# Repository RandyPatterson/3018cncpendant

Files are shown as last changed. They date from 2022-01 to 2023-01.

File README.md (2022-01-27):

# Pendant Controller for 3018 CNC
An Arduino based Handwheel Pendant for a generic 3018 CNC.  Allows you to easily move the X, Y and Z axis using the handwheel.  You can dial in the exact position using the 0.1 mm/step or quickly move to a new location using the 1.0 mm/step buttons.

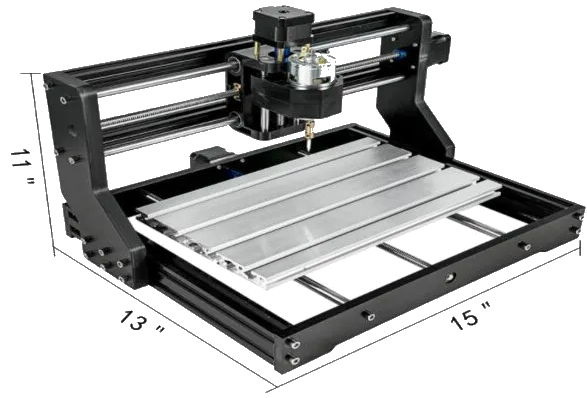
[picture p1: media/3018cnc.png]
3018 CNC

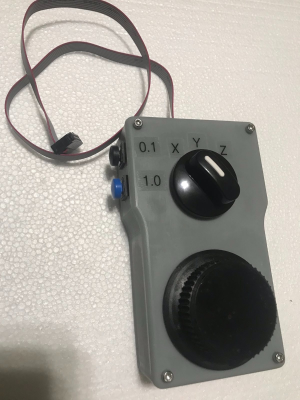
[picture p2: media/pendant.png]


### Required Hardware
1. 1x Arduino Pro Mini (or compatible)
1. 1x KY-040 Rotary Encoder ([Amazon](https://www.amazon.com/gp/product/B07D356LRH/ref=ppx_yo_dt_b_asin_title_o04_s00?ie=UTF8&psc=1))
1. 1x SP3T Rotary Switch ([Amazon](https://www.amazon.com/gp/product/B018LYU3OO/ref=ppx_yo_dt_b_asin_title_o01_s00?ie=UTF8&psc=1))
1. 4x M3 x 6mm screws
1. 4x M3 x 5mm x 3mm thread inserts ([Amazon](https://www.amazon.com/cSeao-120pcs-Inserted-Knurled-Embedded/dp/B07D683Q26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]))
1. 2x 12mm momentary SPST square push buttons
1. 1x 2x4 (8 pin) 2.54mm pitch flat ribbon cable
1. 1x 2x4 2.54mm pitch connector (optional, for PCB) ([Amazon](https://www.amazon.com/gp/product/B07WPBQPBT/ref=ppx_yo_dt_b_asin_title_o03_s00?ie=UTF8&psc=1))

### This repo includes
1. [/src](/src) = Source code for an Arduino Pro Mini (PlatformIO)
1. [/pcb](/pcb) = Schematic and PCB layout (KiCad)
1. [/model](/model) = STEP, Fusion360 and 3MF files for 3D printing the case and handwheel

## Source Code
Build using the PlatformIO plugin for VS Code.  Targeting Arduino Pro Mini but any board can be used as long as it has at least 7 open IO Ports

## Schematic (Optional) 
Optional schematic and PCB to help cleanup the wiring.  Bypass capacitors are used on the encoder data lines to help reduce switch bounce.

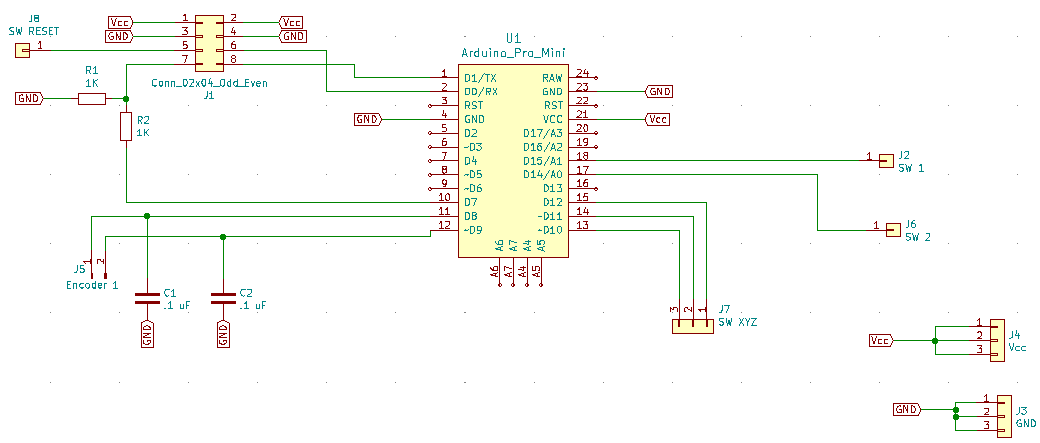
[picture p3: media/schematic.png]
Schematic

### PCB
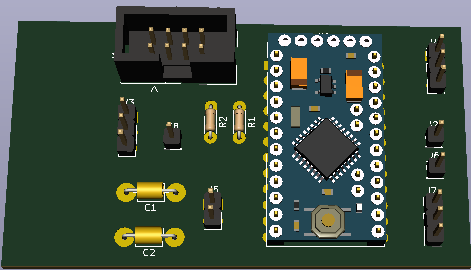
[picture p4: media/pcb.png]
Circuit


## Models
3D Models for case and handwheel to 3D print.  I used a resin printer but the models should be easily printable on FDM Printers.  The Models directory includes the SMF files to print unmodified and STEP files included for situations where you want to modify the 3D models in your favorite CAD program.  Fusion 360 files also included.

### Case & Handwheel Models

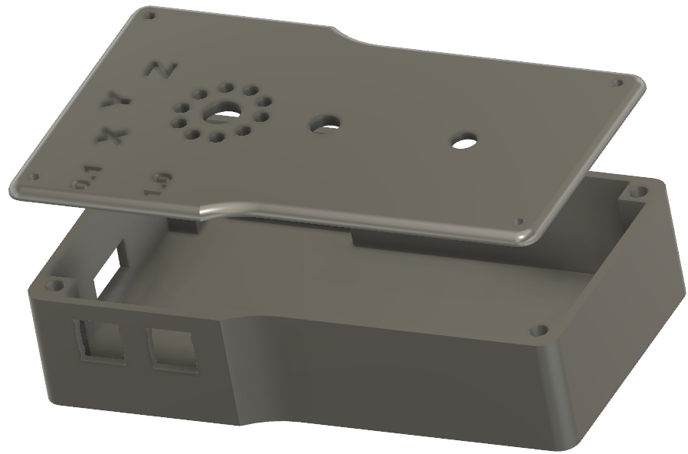
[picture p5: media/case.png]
Case
 
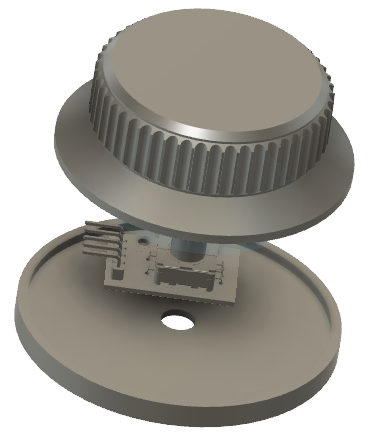
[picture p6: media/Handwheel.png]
Handwheel


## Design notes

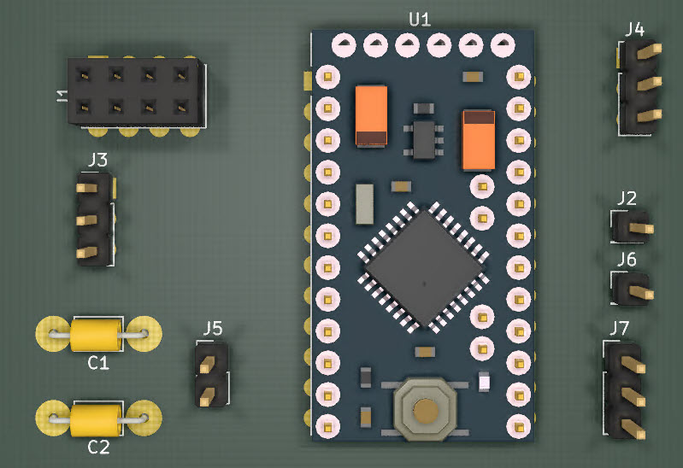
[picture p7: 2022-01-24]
media/circuit_3d.jpg

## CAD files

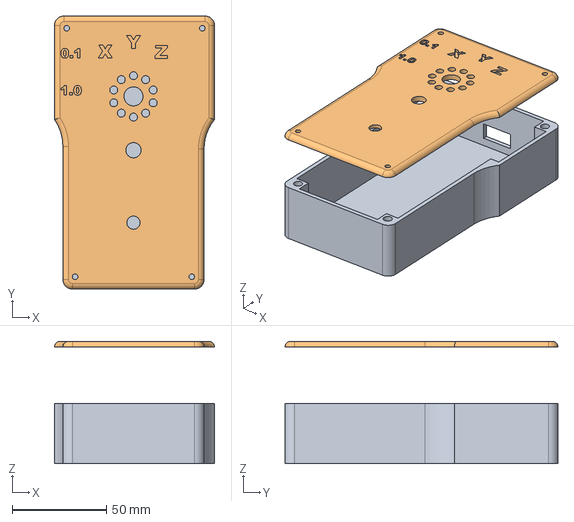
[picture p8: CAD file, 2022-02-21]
models/case/3018 pendant case.step
85.0 x 145.0 x 65.0 mm

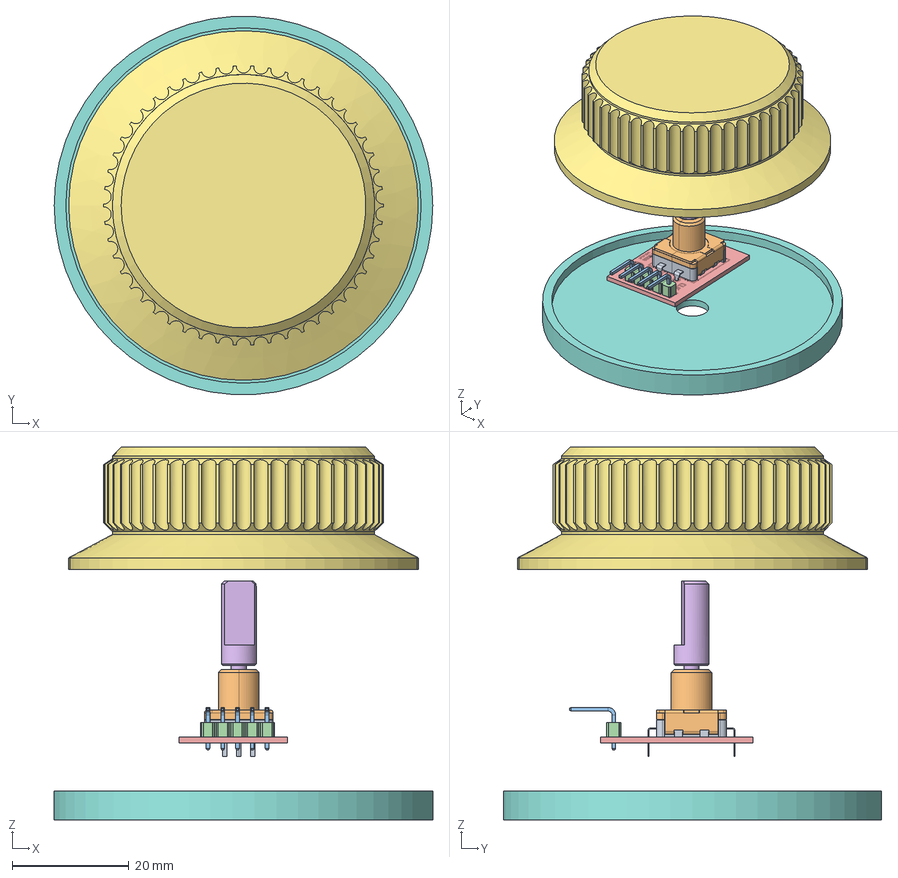
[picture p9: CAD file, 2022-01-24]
models/handwheel/Handwheel.step
65.0 x 64.9 x 64.0 mm
Rotary Encoder
2.54 5PIN 90
pcb
D-handle

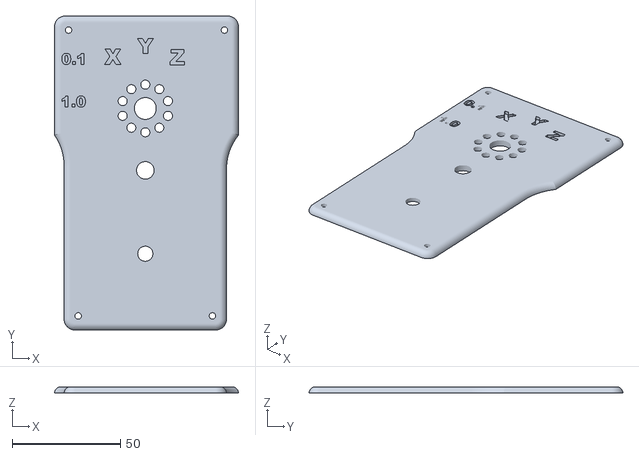
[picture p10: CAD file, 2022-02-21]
models/case/Top.stl
85.0 x 145.0 x 3.00

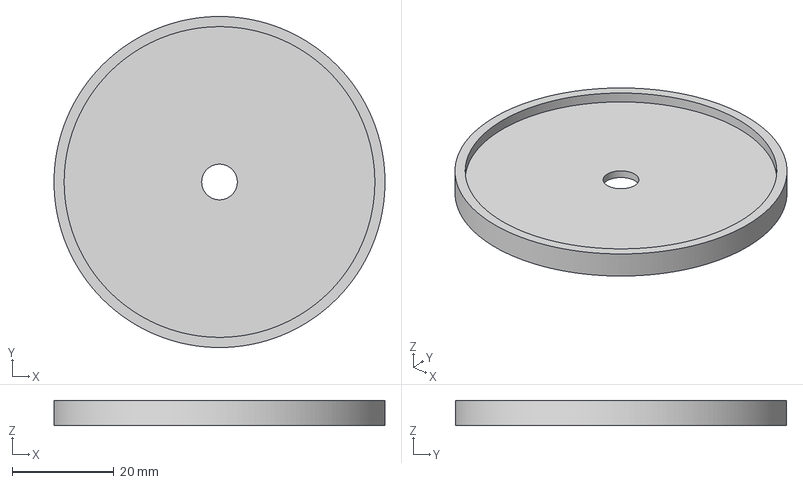
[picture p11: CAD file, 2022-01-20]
models/handwheel/base.3mf
65.0 x 65.0 x 5.00 mm

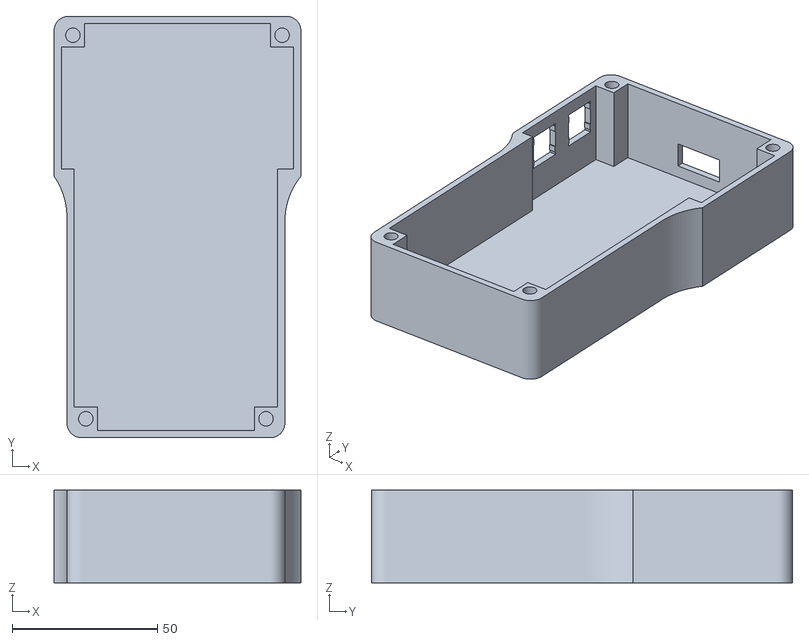
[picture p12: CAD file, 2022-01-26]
models/case/Bottom.stl
85.0 x 145.0 x 32.0

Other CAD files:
models/case/3018 pendant case.f3d
models/handwheel/Handwheel.3mf
models/handwheel/Handwheel.f3d
models/handwheel/Handwheel.stl
models/handwheel/base.stl

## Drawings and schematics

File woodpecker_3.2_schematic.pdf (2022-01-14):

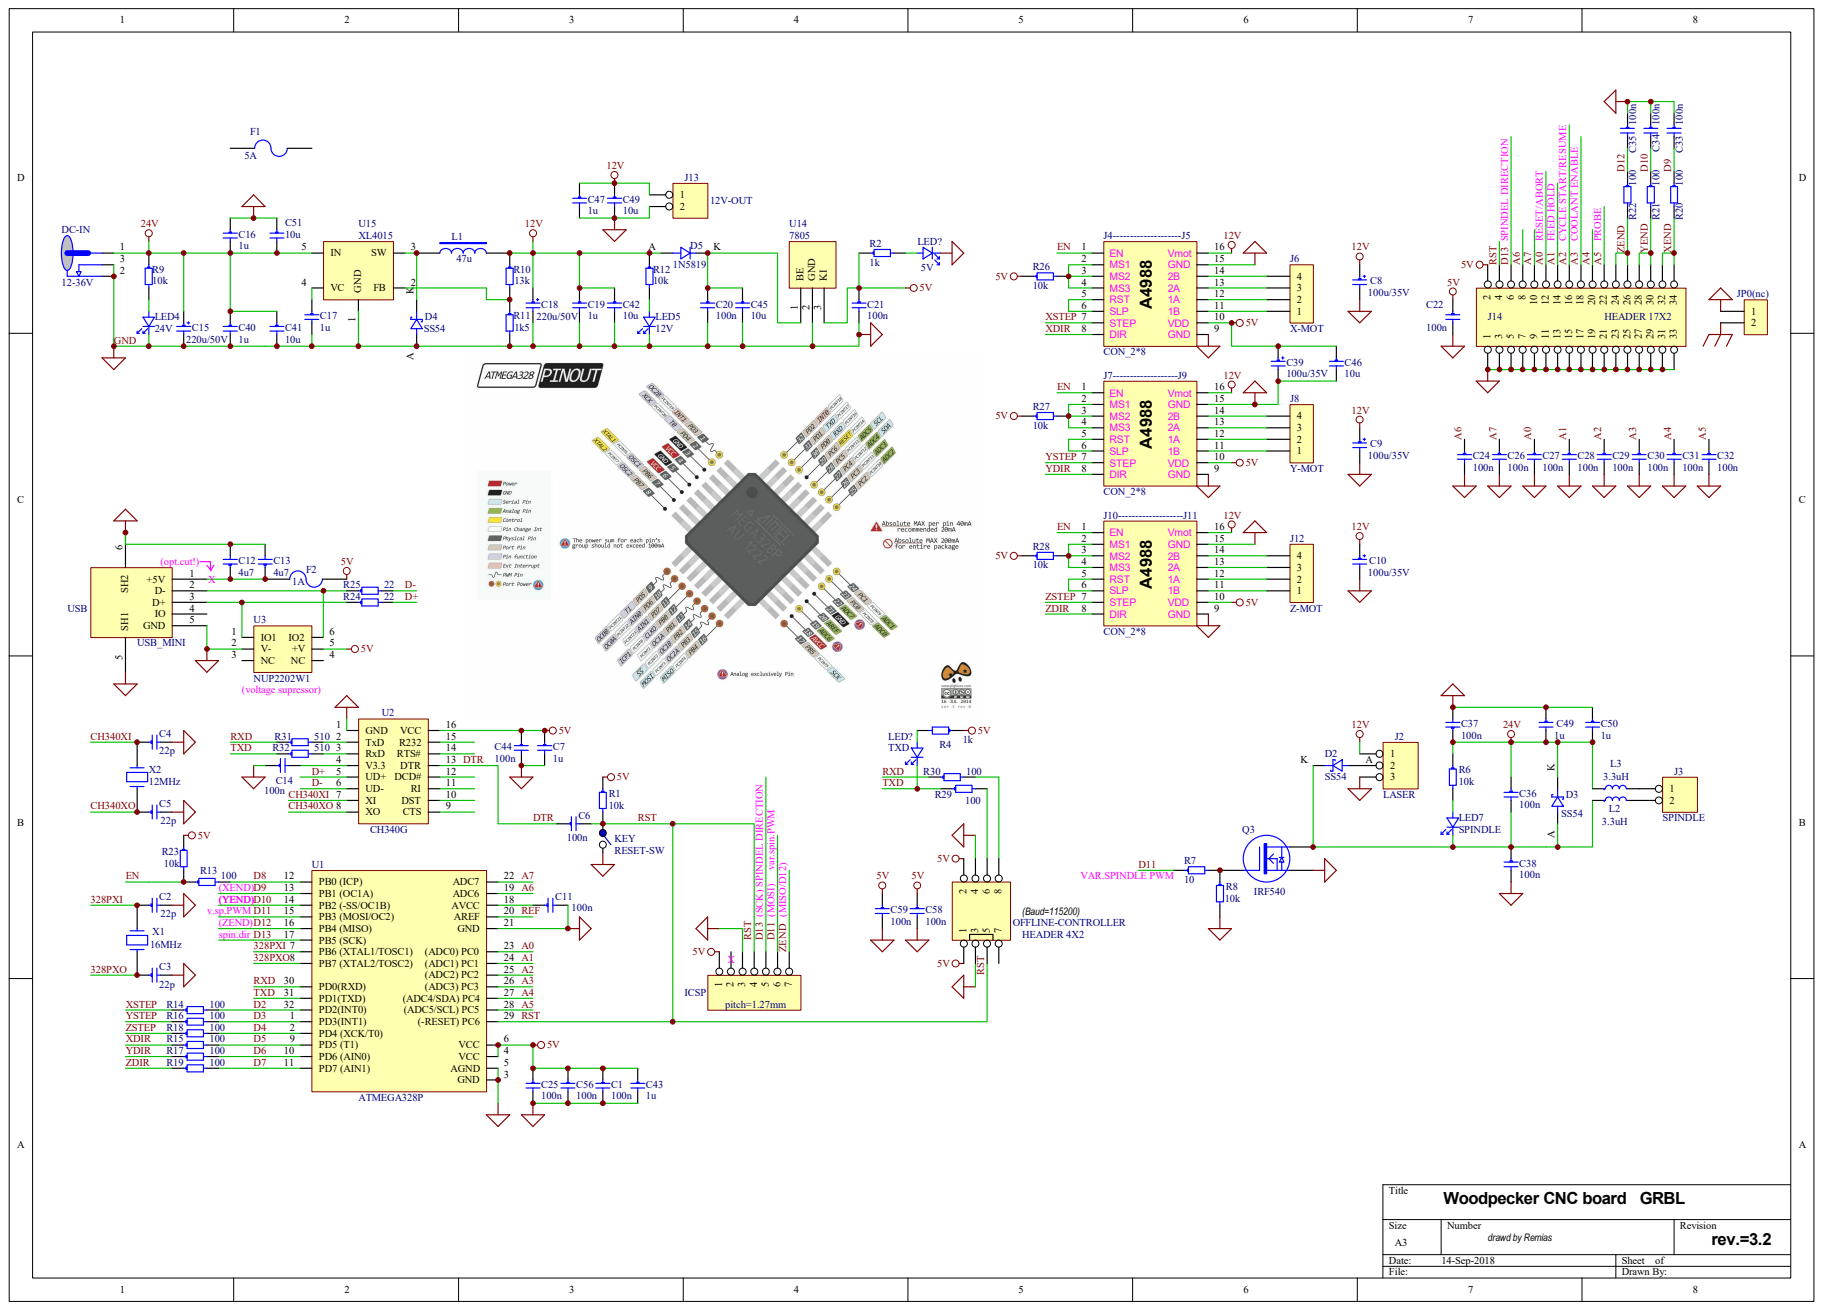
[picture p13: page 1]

Woodpecker CNC board GRBL

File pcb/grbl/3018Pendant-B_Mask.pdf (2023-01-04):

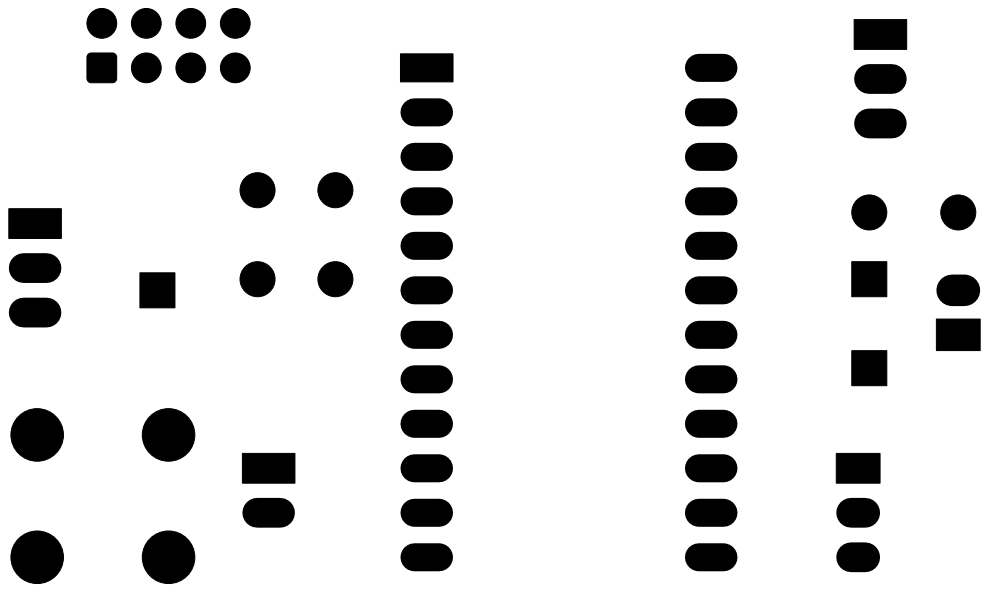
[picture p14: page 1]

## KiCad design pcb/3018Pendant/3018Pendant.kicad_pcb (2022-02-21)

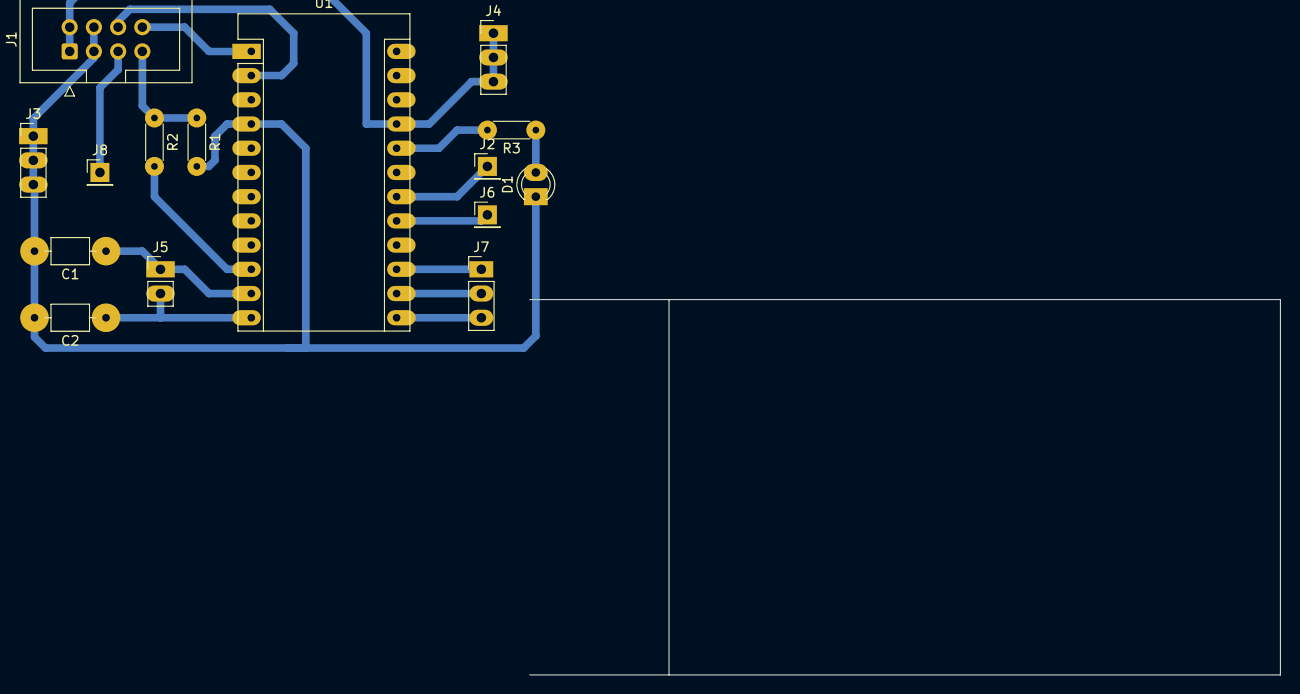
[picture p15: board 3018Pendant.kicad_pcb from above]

Board: 2 copper layers, 78.7 x 39.4 mm, 15 parts (0 on the bottom side), 16 nets.

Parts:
C1, C2: .1 uF; C_Axial_L3.8mm_D2.6mm_P7.50mm_Horizontal
D1: LED; LED_D3.0mm_Clear
J1: Conn_02x04_Odd_Even; IDC-Header_2x04_P2.54mm_Vertical
J2: SW 1; PinHeader_1x01_P2.54mm_Vertical
J3: GND; PinHeader_1x03_P2.54mm_Vertical
J4: Vcc; PinHeader_1x03_P2.54mm_Vertical
J5: Encoder 1; PinHeader_1x02_P2.54mm_Vertical
J6: SW 2; PinHeader_1x01_P2.54mm_Vertical
J7: SW XYZ; PinHeader_1x03_P2.54mm_Vertical
J8: SW RESET; PinHeader_1x01_P2.54mm_Vertical
R1, R2, R3: 1K; R_Axial_DIN0204_L3.6mm_D1.6mm_P5.08mm_Horizontal
U1: Arduino_Pro_Mini; Arduino_Pro_Mini_copy

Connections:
GND: C1.2, C2.2, D1.1, J1.3, J1.4, J3.1, J3.2, J3.3, R1.2, U1.4, U1.23
unnamed: C1.1, J5.1, U1.11
unnamed: C2.1, J5.2, U1.12
unnamed: D1.2, R3.1
unnamed: J1.5, J8.1
unnamed: J1.6, U1.2
unnamed: J1.7, R1.1, R2.1
unnamed: J1.8, U1.1
unnamed: J2.1, U1.18
unnamed: J6.1, U1.17
unnamed: J7.1, U1.15
unnamed: J7.2, U1.14
unnamed: J7.3, U1.13
unnamed: R2.2, U1.10
unnamed: R3.2, U1.20
Vcc: J1.1, J1.2, J4.1, J4.2, J4.3, U1.21

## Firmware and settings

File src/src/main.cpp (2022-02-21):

#include <Arduino.h>


//CNC Parameters
// enter $$ to view parameters
#define x_max_feed_rate 1000 // mm/min $110=
#define y_max_feed_rate 1000 // mm/min $111=
#define z_max_feed_rate 600 // mm/min  $112=


//encode pins 
#define clk_pin       8
#define dx_pin        9
//Move 1 mm
#define distanceA_pin 15
//Move .1 mm
#define distanceB_pin 14

#define x_button_pin  10
#define y_button_pin  11
#define z_button_pin  12

#define usb_busy_pin 7
#define led_green 17


int clk_prev=1;
unsigned long previousMillis = 0;
//How long the current CNC move command will take to coplete
unsigned long delay_in_ms = 0;
//used to determin how long ago (in ms) the encode changed states.  If it's too short ignore it (noise)
unsigned long encoder_prev_millis = 0;
int encoder_prev_val;

/********************************************
Increment: when clk edge falls dx is high
       ____
      |    |
clk __|    |___
         ____ 
        |    |
dx   ___|    |___


Decrement: when clk edge falls and  dx is low
         ____ 
        |    |
clk ____|    |___
      ____
     |    |
dx __|    |___

Returns: 
-1 = encoder turned counter-clockwise (decrement)
 0 = no change 
+1 = encoder turned clockwise (increment)
*********************************************/
int encoder_update() {
  int ret_val = 0;
  int clk = digitalRead(clk_pin);
  unsigned long current_millis = millis();
  unsigned long elapsed = current_millis - encoder_prev_millis;

  //transition from high to low
  if ( clk_prev ==1 &&  clk == 0) { 
    int dt = digitalRead(dx_pin);    
    ret_val = dt==0 ? -1 : 1;
    encoder_prev_millis = current_millis;
    //if less than 50ms elapsed since last encoder change and the encoder 
    //changed directions then ignore it, probably noise
    if (elapsed < 50 && encoder_prev_val != ret_val ) {
        ret_val = 0;
    } 
    else {
      encoder_prev_val = ret_val;
    }
  }
  clk_prev = clk;
  return ret_val;
}


void setup() {
  pinMode(clk_pin,INPUT);
  pinMode(dx_pin,INPUT);

  pinMode(x_button_pin,INPUT_PULLUP);
  pinMode(y_button_pin,INPUT_PULLUP);
  pinMode(z_button_pin,INPUT_PULLUP);
  pinMode(distanceA_pin,INPUT_PULLUP);
  pinMode(distanceB_pin,INPUT_PULLUP); 

  pinMode(usb_busy_pin,INPUT); 
  pinMode(led_green,OUTPUT);

  digitalWrite(led_green,!digitalRead(usb_busy_pin));

  clk_prev = digitalRead(clk_pin);
}

static int prev_busy = 0;
void loop() {



  
  //is high if pc plugged into CNC USB
  int is_usb_busy = digitalRead(usb_busy_pin);
  if (prev_busy != usb_busy_pin) digitalWrite(led_green,!is_usb_busy);

  unsigned long currentMillis = millis();
  unsigned long elapsedMillis = currentMillis - previousMillis;

  int enc_val = encoder_update();
  if (enc_val != 0 && elapsedMillis >= delay_in_ms  && is_usb_busy == LOW ) {
    

    int feedRate = 0;
    char axis = 'X';
    float distance = 0;

    //determin axis to move and feedrate
    if (digitalRead(x_button_pin) == 0) { 
      axis = 'X'; 
      feedRate = x_max_feed_rate;
    } else if (digitalRead(y_button_pin) == 0) { 
      axis = 'Y';
      feedRate = y_max_feed_rate;
    }
    else if (digitalRead(z_button_pin) == 0) { 
      axis = 'Z';
      feedRate = z_max_feed_rate;
    }

    if (digitalRead(distanceA_pin) == 0) distance = 1.0;

    if (digitalRead(distanceB_pin) == 0) distance = 0.1;

    if (feedRate > 0 && distance > 0.0 ) {
      //create command to send to CNC
      String cmd = "$J=G21G91";
      cmd.concat(axis);
      //determine direction based on encoder direction 
      if (enc_val == -1) {
        cmd.concat('-');
      }
      cmd.concat(distance);
      cmd.concat('F');
      cmd.concat(feedRate);
      
      Serial.begin(115200);     
      Serial.println(cmd);
      Serial.end();      
  
    }
    // save the last time you sent a command
    previousMillis = currentMillis;

    prev_busy = is_usb_busy;

    //only send commands after the last one completed
    //calculate how long it will take for CNC to complete this command in ms
    //Distance in mm and feed rate is mm/min.  60000 is the # of milliseconds in a minute
    delay_in_ms = distance / (float)feedRate * 60000;

  }
  
}

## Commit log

2022-01-20 added XYZ to code
    [Handwheel.3mf, base.3mf]
2022-01-24 initial state
    [3018Pendant.kicad_pcb, 3018Pendant.sch, Bottom.3mf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]
2022-01-26 update to files
    [Bottom.3mf, Bottom.stl, Bottom_small.3mf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]
2022-01-27 add code to detect USB Device connected
2022-01-27 Update schematic & PCB to include reset button
    [3018Pendant.kicad_pcb, 3018Pendant.sch]
2022-01-27 Add LED
    [3018Pendant.kicad_pcb, 3018Pendant.sch]
2022-02-21 final version
    [3018Pendant.kicad_pcb, Top-2.3mf, Top.3-3mf.3mf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]
2022-02-21 update docs
    [3018 pendant case.f3d, 3018 pendant case.step, Bottom.3mf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]
2023-01-04 minor docs update
    [3018Pendant.kicad_sch]
